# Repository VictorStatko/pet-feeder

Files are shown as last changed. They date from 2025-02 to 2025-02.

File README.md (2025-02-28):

# Pet Feeder

This project allows you to build an automated 3d printed pet feeder using an ESP32 microcontroller. It runs on a parallel 18650 battery pack. In my case, it works for about 2 months on a single charge. It supports scheduled feeding based on specified times and portion weights, sends Telegram notifications about all activities, and provides updates on the device's status, including battery percentage.

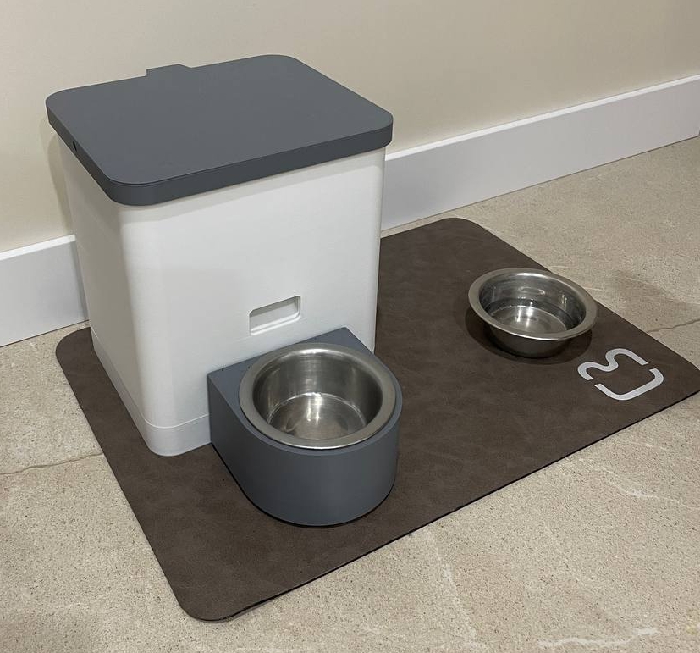
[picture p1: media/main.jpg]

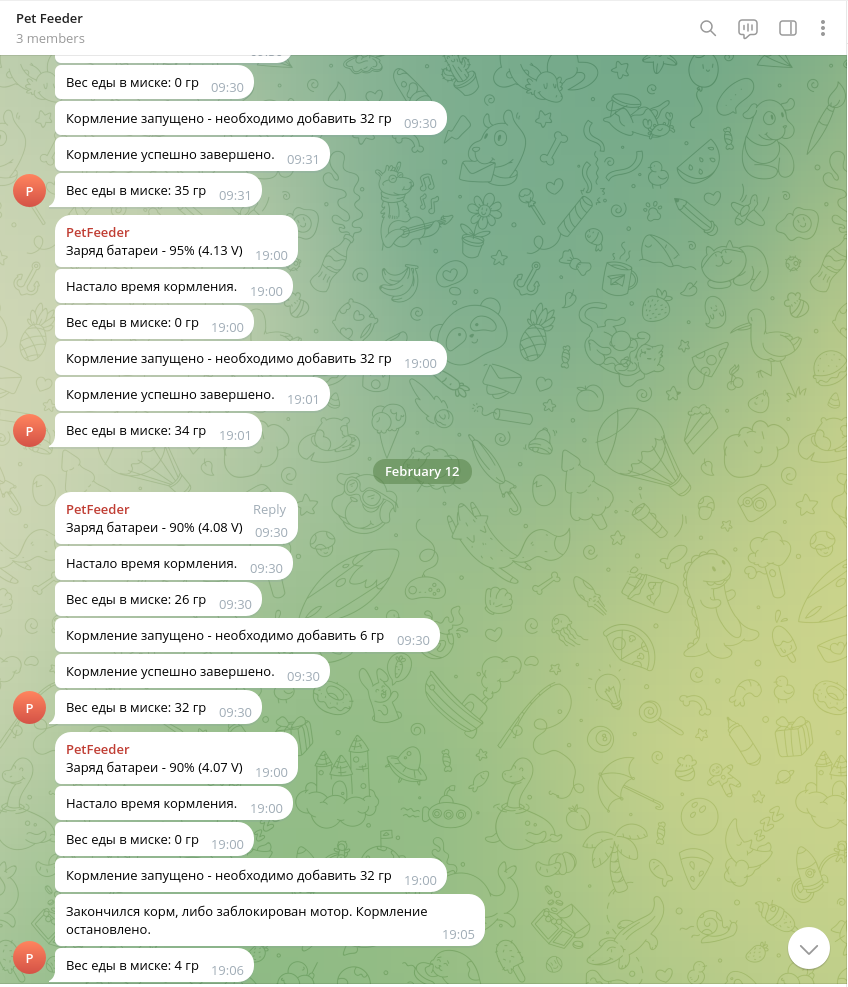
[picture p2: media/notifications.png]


https://github.com/user-attachments/assets/1bdc0e0a-baae-4a7a-a652-37525bfb75da

The approximate size of the feeder is 210 mm (width) x 180 mm (depth) x 240 mm (height). These dimensions can be modified as needed. All relevant files are included below.

In this configuration, the feeder holds approximately 1 kg of small-breed dog food.

## Hardware

1. ESP32 C3 (I used [TENSTAR ROBOT ESP32-C3](https://sl.aliexpress.ru/p?key=hEJPGh3))
2. DRV8833 DC Motor Driver (I used [WAVGAT DRV8833 Dual Motor Driver 1A](https://sl.aliexpress.ru/p?key=jnJPG1g))
3. DC Motor - 6V or lower (I used [JGA25-310 6V 20 RPM](https://sl.aliexpress.ru/p?key=jvJPGnO))
4. HX711 Weight Sensor + Load Cell (I used [1 KG load cell](https://sl.aliexpress.ru/p?key=o0JPGWY))
5. DS1302 RTC Module
6. Voltage Boost Converter (Something like the MT3608 will work, but I used a [UPS module](https://sl.aliexpress.ru/p?key=qwMPGBO) since I had a couple on hand)
7. Voltage Sensor (I used a [separate module](https://sl.aliexpress.ru/p?key=GOMPG0S), but just a couple of resistors would also work)
8. Power switch (I used a [double-pole switch](https://sl.aliexpress.ru/p?key=SGMPGXe) because I had it, but a simpler option would work too)
9. 18650 Parallel Pack Holder
10. Type-C Connector to power ESP32 C3 (Optional because there are other options, but I find it convenient to use)
11. Wago Connectors (Optional, but works for me - so why not)

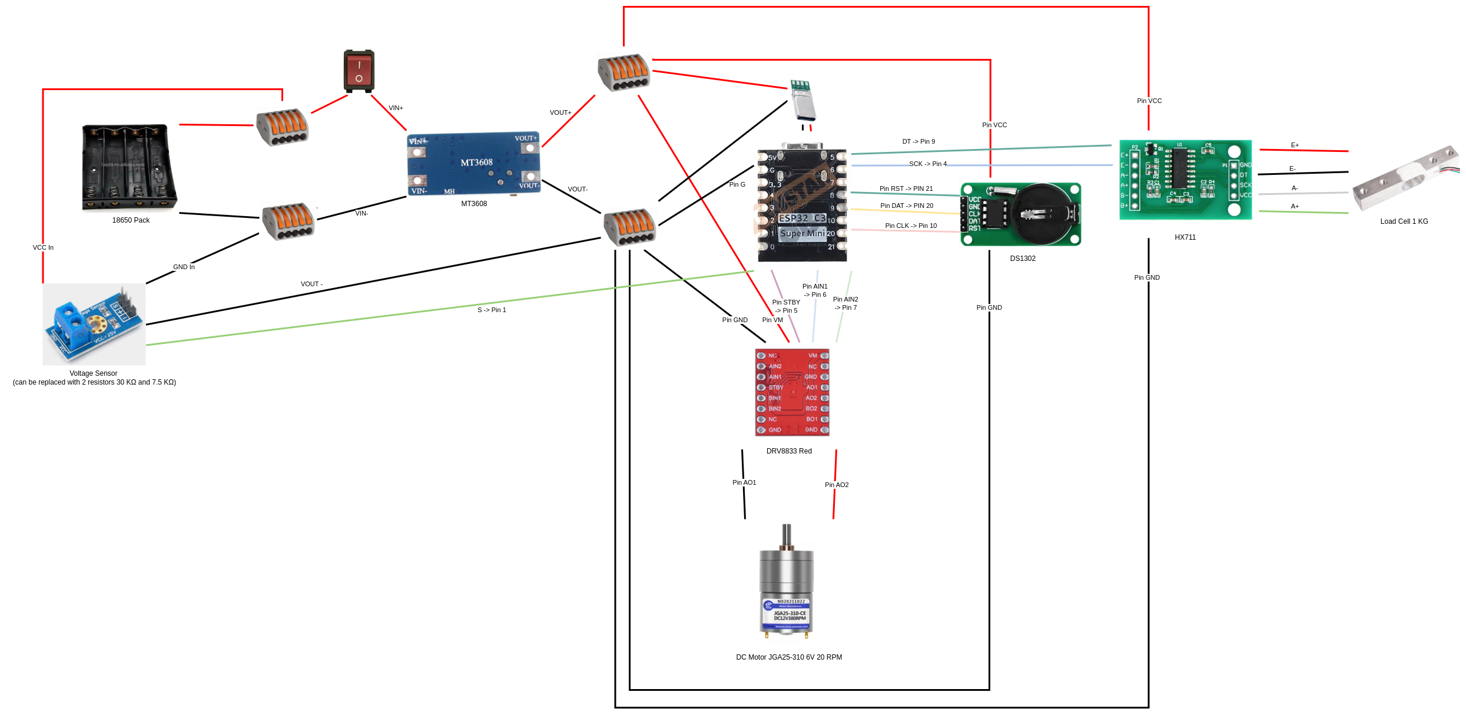
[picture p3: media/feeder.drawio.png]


## Model

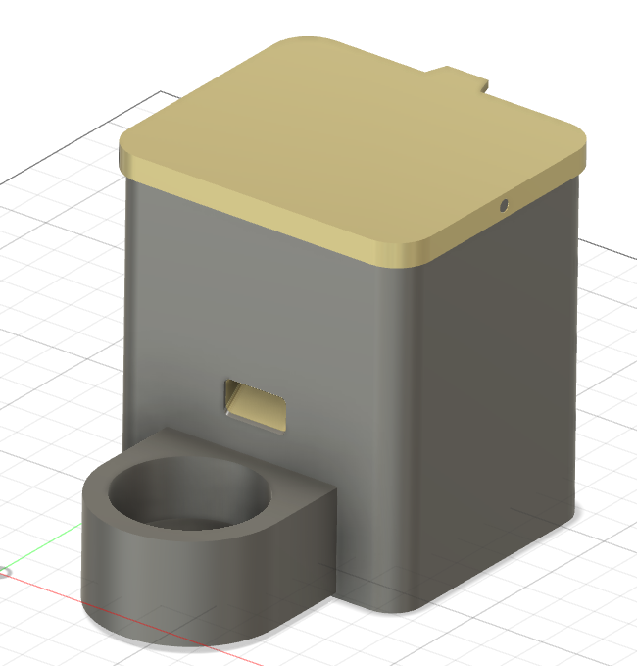
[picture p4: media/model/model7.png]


First of all, many thanks to Alexander Ulitin (https://github.com/ulitiy).

Initially, I planned to design the project from scratch, but I realized I was a bit lazy. So, I came across his awesome project (https://cubebrush.co/momwillbeproud/products/ndqc7a-5FoB/ultimate-3d-printed-pet-feeder) and decided to redesign it to better suit my needs.

Fusion file of redesigned project: [feeder.f3d](media/feeder.f3d)

Some screenshots can be found here: [model](media/model)

## Printed Parts

The feeder was printed using an Ender 3 V3 KE, which has a print size of 220 mm x 220 mm. Manual supports were used during the printing process. For additional hints and details about the printing process, please refer to the pictures here: [printedParts](media/printedParts)

## Assembly

Assembly photos can be found here: [assembly](media/assembly)

## Software

### 1. Install Arduino IDE
Set up the [Arduino IDE for ESP32](https://docs.espressif.com/projects/arduino-esp32/en/latest/installing.html) by following the official instructions.

### 2. Configure Partition Scheme
In the Arduino IDE, navigate to:
- **Tools** -> **Partition Scheme** -> **Huge App**.

### 3. Define Pins Used by the Feeder
Update the pin configuration in `feeder/UsedPins.h` according to your hardware setup.

### 4. Calibrate Load Cell (Step 1)
1. Open the file `additional/loadCellCalibration1` in the Arduino IDE.
2. Upload the sketch to the ESP32 and follow the Serial Monitor instructions.
3. Calculate the calibration factor using the formula:
   ```
   calibration factor = (reading) / (known weight)
   ```  
4. Save this calibration factor (e.g., `1106`).

### 5. Calibrate Load Cell (Step 2)
1. Open the file `additional/loadCellCalibration2` in the Arduino IDE.
2. Upload the sketch to the ESP32.  
   Perform this step after embedding the load cell into the 3D-printed enclosure (including the plate, but excluding the bowl).
3. Save the offset value obtained (e.g., `-62230`).

### 6. Configure Load Cell in Code
Include the retrieved calibration values in your code as follows:
```cpp
WeightSensor weightSensor(LOADCELL_DOUT_PIN, LOADCELL_SCK_PIN, 1106, -62230);
```

### 7. (Optional) Change Messages

Currently, all notification messages are provided only in Russian. If you want, you can change them - everything is in a single file:

**feeder/Messages.h**

### 8. Explore Additional Examples
In the `additional` folder, you’ll find example sketches for:
- **DC Motor Control**: Demonstrates how to control the motor used for dispensing food.
- **Load Cell**: Includes further examples for advanced load cell usage and testing.

Use these examples to better understand and customize specific components of the feeder.

### 9. Create a Telegram Bot
1. Open Telegram and search for **BotFather**.
2. Start a chat with **BotFather** and send the command `/newbot`.
3. Follow the instructions to set up your bot. You’ll receive a bot token upon completion.

### 10. Create a Telegram Group and Retrieve Group ID
1. Create a new Telegram group.
2. Add your bot and **@getidsbot** to the group.
3. Wait for **@getidsbot** to post a message containing the group ID. Copy the ID, then remove **@getidsbot** from the group.

### 11. Upload Code to ESP32
1. Open the main sketch for your feeder project in the Arduino IDE.
2. Connect your ESP32 to your computer via USB.
3. Select the correct **Board** and **Port** in the Arduino IDE:
   - **Tools** -> **Board** -> **ESP32 Dev Module**
   - **Tools** -> **Port** -> Select your ESP32's port.
4. Click **Upload** to flash the code onto your ESP32.

### 12. Connect ESP32 to Wi-Fi and Configure Feeder
1. When powered on, the ESP32 will broadcast an access point named **PetFeeder** with the password **11111111**.
2. Connect to this access point within 5 minutes to access the configuration portal.
3. Go to 192.168.4.1
4. Fill in the following details:
   - Wi-Fi credentials
   - Telegram bot token
   - Telegram group ID
   - Feeding schedule and portion weights

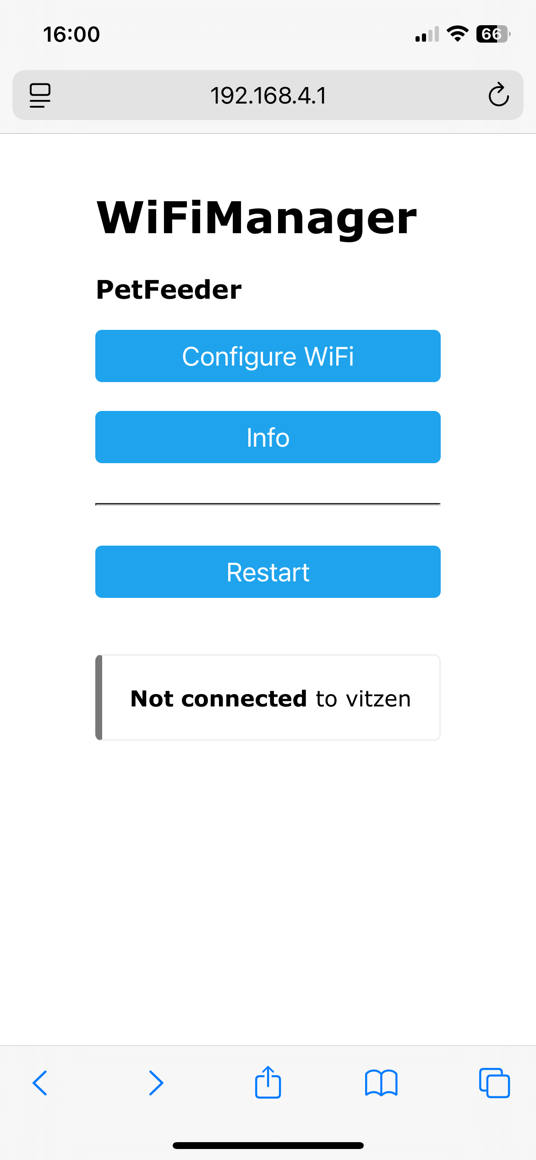
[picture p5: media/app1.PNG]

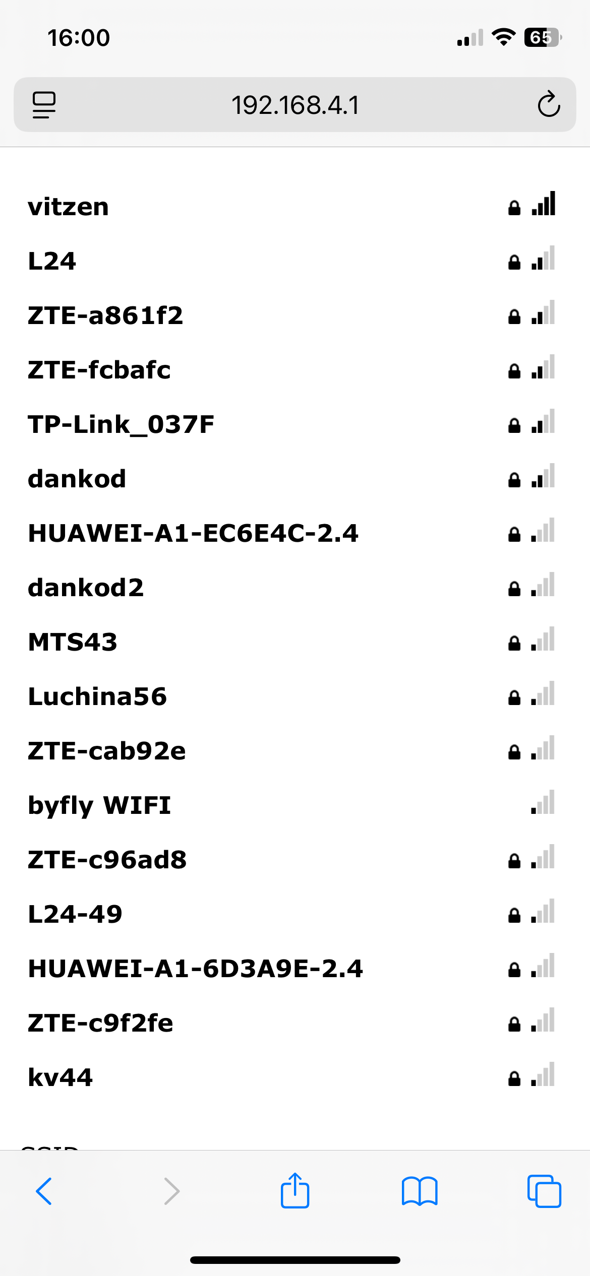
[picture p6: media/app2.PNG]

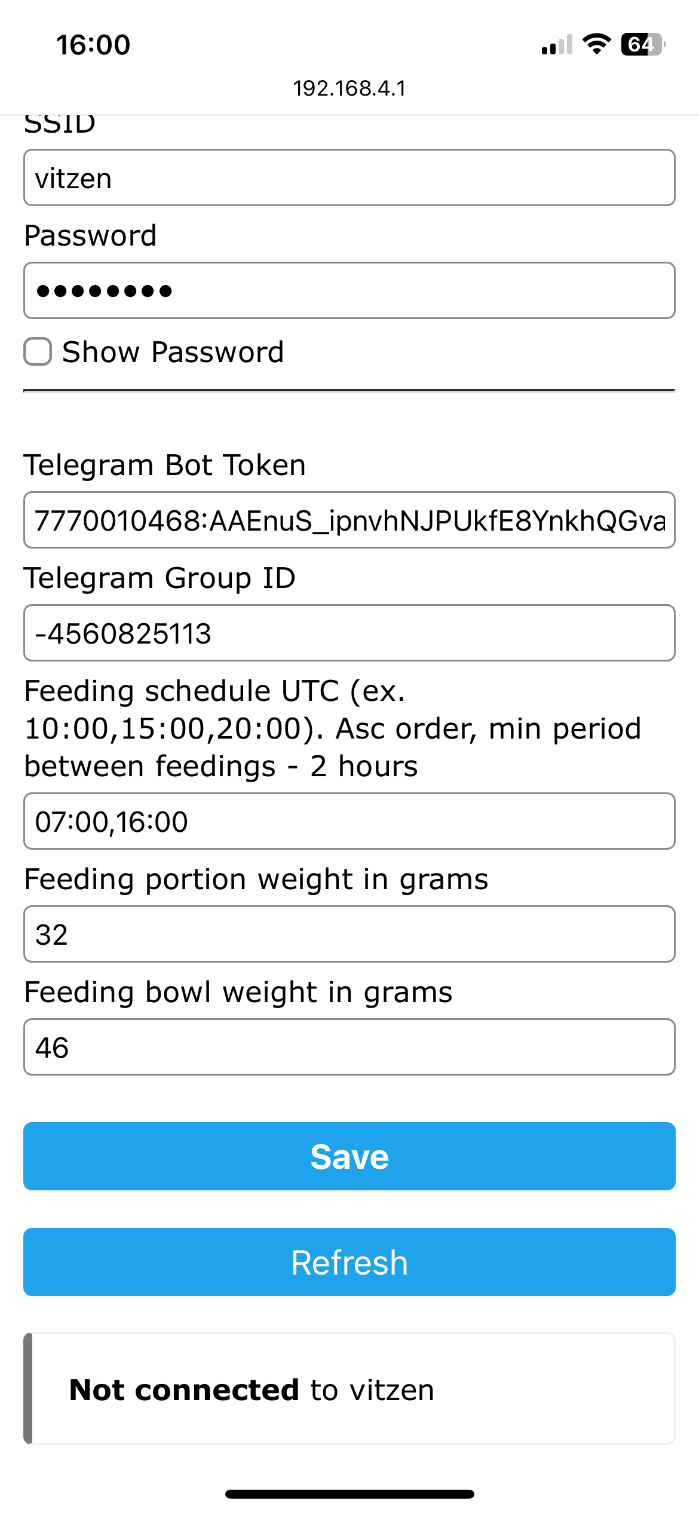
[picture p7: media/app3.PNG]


Once configured, the ESP32 will connect to Wi-Fi. You’ll receive a welcome message in your Telegram group either immediately upon successful connection or after the 5-minute configuration window expires.

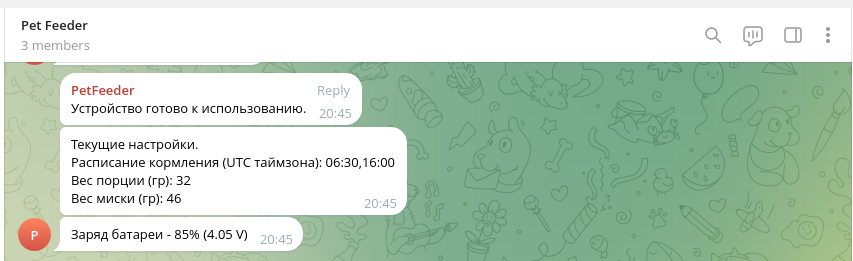
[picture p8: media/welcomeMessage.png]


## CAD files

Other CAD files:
media/feeder.f3d

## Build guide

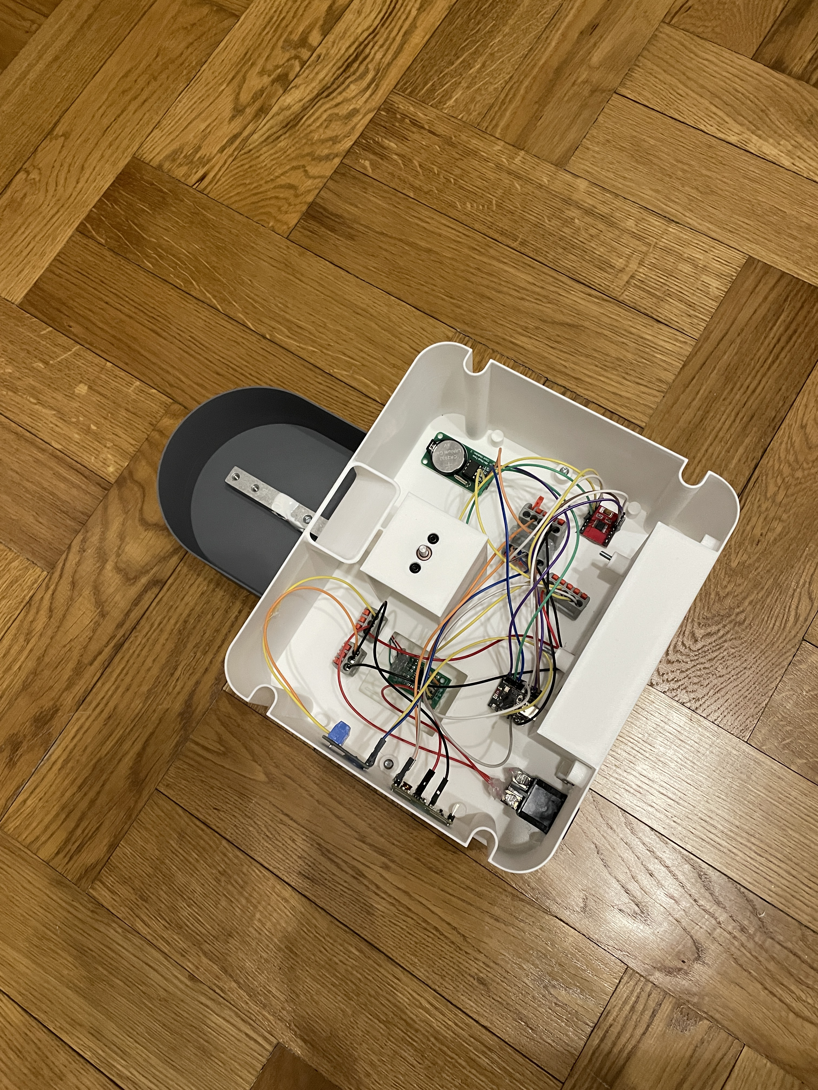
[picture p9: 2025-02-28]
media/assembly/4.JPG

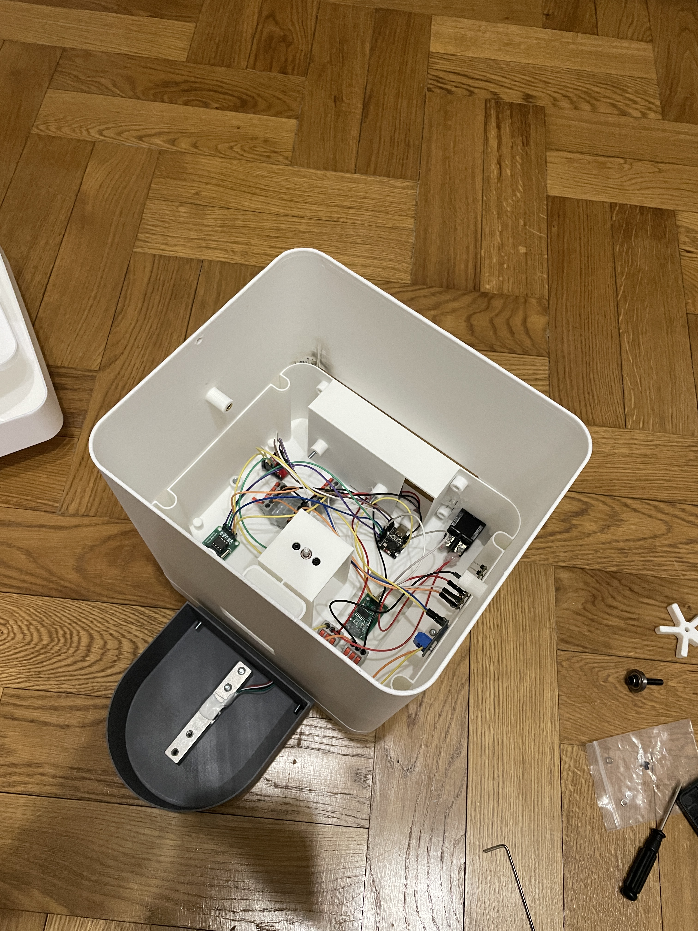
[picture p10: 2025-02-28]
media/assembly/6.JPG

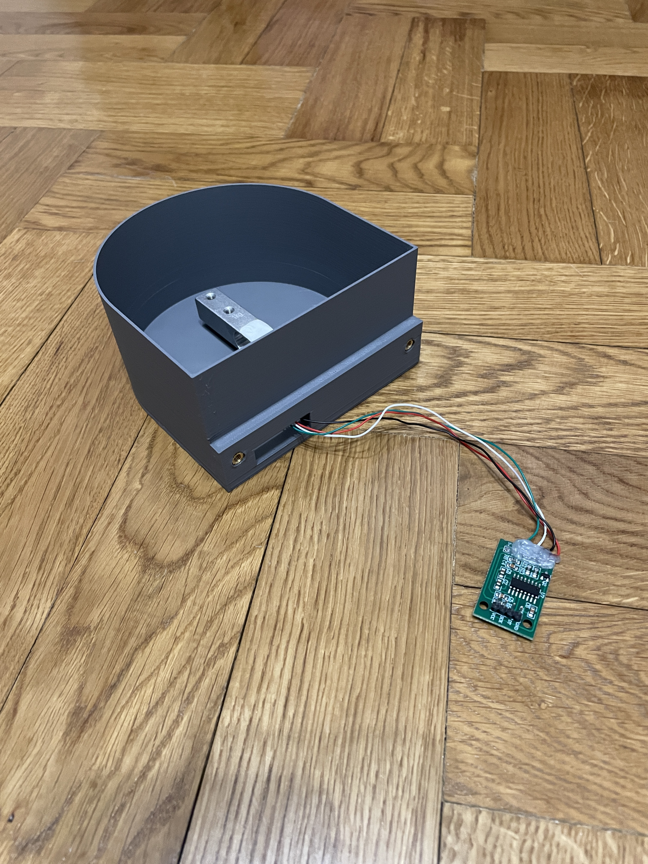
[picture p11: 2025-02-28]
media/assembly/1.JPG

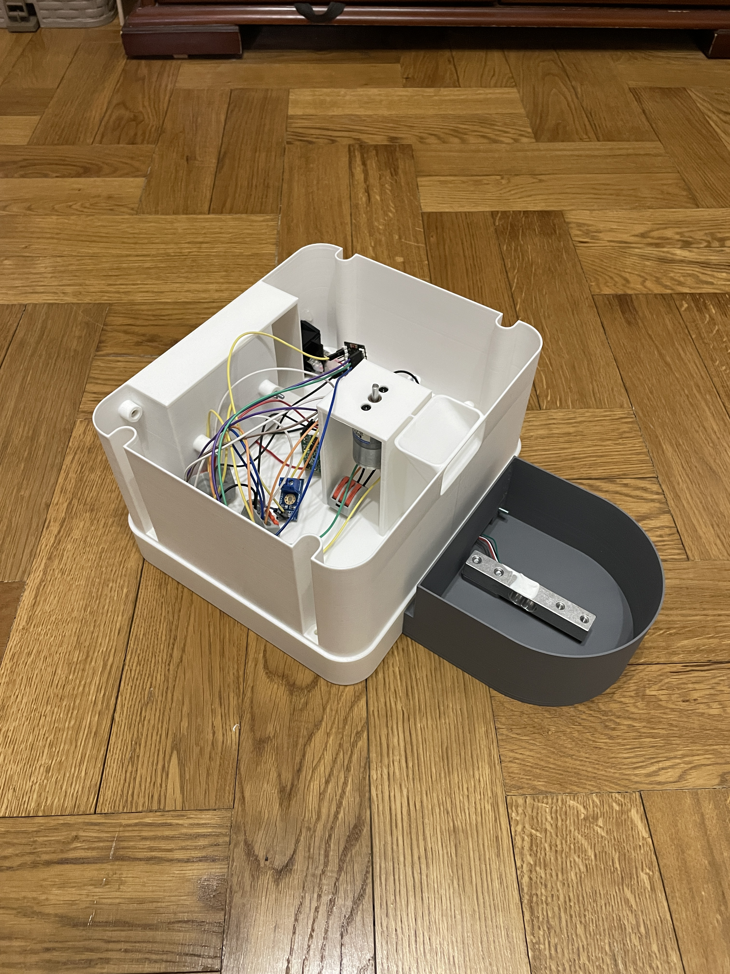
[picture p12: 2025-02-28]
media/assembly/3.JPG

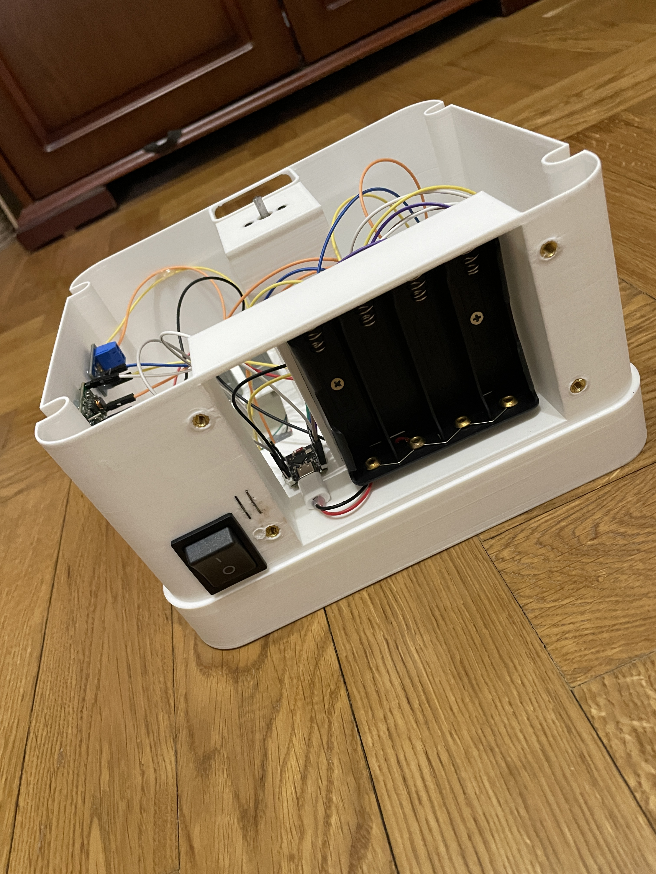
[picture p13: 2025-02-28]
media/assembly/5.JPG

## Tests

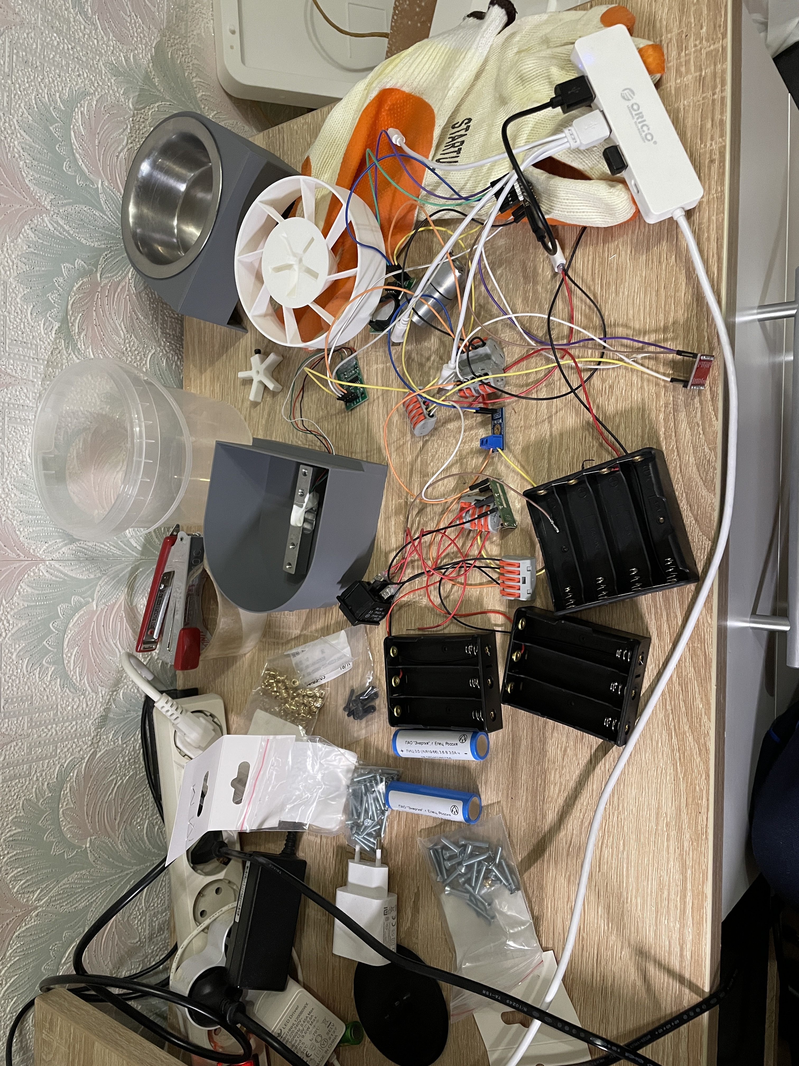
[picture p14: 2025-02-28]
media/assembly/testStand.JPG

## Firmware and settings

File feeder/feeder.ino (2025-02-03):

#include <Arduino.h>
#include "WiFiManagerWrapper.h"
#include "TelegramHandler.h"
#include <WiFi.h>
#include "ScheduleHandler.h"
#include "PreferencesHandler.h"
#include "VoltageSensor.h"
#include "WeightSensor.h"
#include "DCMotor.h"
#include "Messages.h"
#include "RtcModule.h"
#include "UsedPins.h"
#include <cmath>

// Persistent variables
RTC_DATA_ATTR bool initialSetupDone = false;

TelegramHandler telegramHandler;
RtcModule rtcModule(RTC_MODULE_DAT_PIN, RTC_MODULE_CLK_PIN, RTC_MODULE_RST_PIN, telegramHandler);
VoltageSensor voltageSensor(VOLTAGE_SENSOR_PIN);
WeightSensor weightSensor(LOADCELL_DOUT_PIN, LOADCELL_SCK_PIN, 1106, -62230);
DCMotor dcMotor(MOTOR_IN1_PIN, MOTOR_IN2_PIN, MOTOR_STBY_PIN);

// Setup function
void setup() {
  Serial.begin(115200);
  delay(1000);  // Allow Serial to stabilize
  Serial.println("Main - Device is waking up...");

  telegramHandler.begin(PreferencesHandler::getBotToken(), PreferencesHandler::getGroupId());
  rtcModule.begin();

  if (!initialSetupDone) {
    Serial.println("Main - Initial setup not done. Launching WiFiManager...");

    WiFiManagerWrapper::setupWiFiManager(telegramHandler);
    Serial.println("Main - WiFiManager setup completed.");

    WiFiManagerWrapper::autoConnectWiFi();
    Serial.println("Main - WiFi connection attempt executed.");

    rtcModule.sync();
    Serial.println("Main - RTC synchronization step executed.");

    telegramHandler.sendBotMessage(MESSAGE_READY_TO_USE);
    telegramHandler.sendBotMessage(
      MESSAGE_CURRENT_SETTINGS + "\n" + MESSAGE_CURRENT_SETTINGS_SCHEDULING + PreferencesHandler::getFeedingScheduleString()
      + "\n" + MESSAGE_CURRENT_SETTINGS_PORTION_WEIGHT + String(PreferencesHandler::getFeedingWeightPerPortion())
      + "\n" + MESSAGE_CURRENT_SETTINGS_BOWL_WEIGHT + String(PreferencesHandler::getFeedingBowlWeight()));
    telegramHandler.sendBotMessage(voltageSensor.getVoltageInfoMessage());

    initialSetupDone = true;
    Serial.println("Main - Initial setup completed and marked as done.");
  } else {
    Serial.println("Main - Initial setup already done. Skipping.");
  }
}

void goToDeepSleep(uint64_t seconds) {
  Serial.println("Main - Going to deep sleep for " + String(seconds) + " seconds...");
  delay(5000);                                       // For serial
  esp_sleep_enable_timer_wakeup(seconds * 1000000);  // Convert seconds to microseconds
  esp_deep_sleep_start();
}

int feedFood(int weightToFeed, int currentWeight) {
  Serial.println("Main - Starting food feeding process...");
  int previousWeight = currentWeight;
  int newWeight = -1;
  float newWeightFloat = -1;
  unsigned long lastWeightChangeTime = millis();

  bool weightSensorError = false;
  bool noWeightChangeError = false;
  bool success = false;

  while (true) {
    dcMotor.startMotor(false);
    delay(300);
    dcMotor.startMotor(true);
    delay(150);
    dcMotor.stopMotor();
    delay(1000);

    newWeightFloat = weightSensor.readWeight();

    if (std::isnan(newWeightFloat)) {
      Serial.println("Main - Error: Weight sensor not ready.");
      weightSensorError = true;
      break;
    } else {
      newWeight = floor(newWeightFloat);
    }

    if (newWeight > previousWeight + 2) {
      lastWeightChangeTime = millis();
      previousWeight = newWeight;
      Serial.println("Main - Weight increased. Updated previous weight: " + String(previousWeight));
    }

    if (millis() - lastWeightChangeTime > 300000) {
      Serial.println("Main - Stopping motor: No significant weight increase in the last 300 seconds.");
      noWeightChangeError = true;
      break;
    }

    if (newWeight >= currentWeight + weightToFeed) {
      Serial.println("Main - Stopping motor: Target weight reached.");
      success = true;
      break;
    }
  }

  if (weightSensorError) {
    telegramHandler.sendBotMessage(MESSAGE_WEIGHT_ERROR + MESSAGE_FEEDING_STOPPED);
    return -1;
  }

  if (noWeightChangeError) {
    telegramHandler.sendBotMessage(MESSAGE_FEEDING_NO_WEIGHT_CHANGE);
  }

  if (success) {
    telegramHandler.sendBotMessage(MESSAGE_FEEDING_SUCCESS);
  }

  return newWeight;
}

void startFeeding(time_t feedingTime) {
  Serial.println("Main - Feeding time! Activating feeder...");
  weightSensor.begin();
  dcMotor.begin();

  WiFiManagerWrapper::autoConnectWiFi();
  Serial.println("Main - WiFi connection attempt executed.");

  telegramHandler.sendBotMessage(voltageSensor.getVoltageInfoMessage());
  telegramHandler.sendBotMessage(MESSAGE_TIME_TO_FEED);

  int bowlWeight = PreferencesHandler::getFeedingBowlWeight();
  int weightPerPortion = PreferencesHandler::getFeedingWeightPerPortion();
  float initialWeightFloat = weightSensor.readWeight();

  if (std::isnan(initialWeightFloat)) {
    Serial.println("Main - Error: Weight sensor not ready.");
    telegramHandler.sendBotMessage(MESSAGE_WEIGHT_ERROR + MESSAGE_FEEDING_MISSED);
  } else {
    int initialWeight = floor(initialWeightFloat);
    int adjustedWeight = max(0, initialWeight - bowlWeight);

    if (initialWeight < bowlWeight / 2) {
      Serial.println("Main - No bowl. Feeding will not be executed.");
      telegramHandler.sendBotMessage(MESSAGE_NO_BOWL);
    } else {
      Serial.println("Main - Current weight of food: " + String(adjustedWeight));
      telegramHandler.sendBotMessage("Вес еды в миске: " + String(adjustedWeight) + " " + MESSAGE_GRAMM);

      int weightToFeed = weightPerPortion - adjustedWeight;

      if (weightToFeed <= 0) {
        Serial.println("Main - Current weight of food is enough. Feeding will be skipped.");
        telegramHandler.sendBotMessage(MESSAGE_FEEDING_ENOUGH_FOOD);
      } else {
        Serial.println("Main - Need to add the following amount of food (in grams): " + String(weightToFeed));
        telegramHandler.sendBotMessage(MESSAGE_FEEDING_START + String(weightToFeed) + " " + MESSAGE_GRAMM);

        int newWeight = feedFood(weightToFeed, initialWeight);

        if (newWeight != -1) {
          telegramHandler.sendBotMessage("Вес еды в миске: " + String(newWeight - initialWeight + adjustedWeight) + " " + MESSAGE_GRAMM);
        }
      }
    }
  }

  PreferencesHandler::saveLastFeedingTime(feedingTime);
  Serial.println("Main - Last feeding time saved.");

  weightSensor.end();
  dcMotor.end();
  Serial.println("Main - Feeding process completed and hardware turned off.");
}

// Main loop
void loop() {
  Serial.println("Main - Checking schedule for feeding time...");
  time_t now = rtcModule.getCurrentTime();

  std::vector<time_t> feedingTimes = ScheduleHandler::parseFeedingSchedule(now);
  time_t feedingTime = ScheduleHandler::shouldFeedNow(feedingTimes, now);

  bool feedNow = feedingTime != 0;

  time_t nextWakeup = ScheduleHandler::calculateNextWakeup(feedingTimes, now, feedNow);

  if (feedNow) {
    Serial.println("Main - Feeding time detected. Starting feeding process...");
    startFeeding(feedingTime);
    rtcModule.sync();
  } else {
    Serial.println("Main - Not feeding time yet. Next wakeup scheduled.");
  }

  goToDeepSleep(nextWakeup - now);
}

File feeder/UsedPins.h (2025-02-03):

#ifndef USED_PINS_H
#define USED_PINS_H

#include <Arduino.h>

const int VOLTAGE_SENSOR_PIN = 1;
const int RTC_MODULE_CLK_PIN = 10;
const int RTC_MODULE_DAT_PIN = 20;
const int RTC_MODULE_RST_PIN = 21;
const int LOADCELL_DOUT_PIN = 9;
const int LOADCELL_SCK_PIN = 4;
const int MOTOR_IN1_PIN = 6;
const int MOTOR_IN2_PIN = 7;
const int MOTOR_STBY_PIN = 5;

#endif

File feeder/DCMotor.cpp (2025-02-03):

#include "DCMotor.h"

DCMotor::DCMotor(int pinIn1, int pinIn2, int pinStby)
  : pinIn1(pinIn1), pinIn2(pinIn2), pinStby(pinStby) {
  Serial.println("DCMotor - Constructor initialized");
}

void DCMotor::begin() {
  Serial.println("DCMotor - Initializing pins and enabling motor standby mode");
  pinMode(pinIn1, OUTPUT);
  pinMode(pinIn2, OUTPUT);
  pinMode(pinStby, OUTPUT);

  digitalWrite(pinStby, HIGH);
  delay(1000);
  Serial.println("DCMotor - Initialization complete");
}

void DCMotor::end() {
  Serial.println("DCMotor - Stopping motor and disabling standby");
  digitalWrite(pinIn1, LOW);
  digitalWrite(pinIn2, LOW);
  digitalWrite(pinStby, LOW);
  Serial.println("DCMotor - Motor and standby disabled");
}

void DCMotor::startMotor(bool reverse) {
  Serial.println("DCMotor - Starting motor (IN1: HIGH, IN2: LOW)");
  if (reverse) {
    digitalWrite(pinIn1, LOW);
    digitalWrite(pinIn2, HIGH);
    Serial.println("DCMotor - Motor started (reverse)");
  } else {
    digitalWrite(pinIn1, HIGH);
    digitalWrite(pinIn2, LOW);
    Serial.println("DCMotor - Motor started");
  }
}

void DCMotor::stopMotor() {
  Serial.println("DCMotor - Stopping motor (IN1: LOW, IN2: LOW)");
  digitalWrite(pinIn1, LOW);
  digitalWrite(pinIn2, LOW);
  Serial.println("DCMotor - Motor stopped");
}

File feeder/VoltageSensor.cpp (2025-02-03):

#include "VoltageSensor.h"
#include "AnalogUtils.h"
#include "Messages.h"

VoltageSensor::VoltageSensor(int pin)
  : pin(pin) {}

float VoltageSensor::readRawVoltage() {
  const int attempts = 10;                  // Number of attempts
  const int readingsPerAttempt = 10;         // Number of readings per attempt
  const int delayBetweenAttemptsMs = 1000;  // Delay between attempts in milliseconds

  float totalVoltage = 0;

  for (int attempt = 0; attempt < attempts; ++attempt) {
    float attemptVoltage = 0;

    // Perform multiple readings for accuracy during this attempt
    for (int reading = 0; reading < readingsPerAttempt; ++reading) {
      int adcValue = AnalogUtils::readValue(pin);
      float adcVoltage = ((float)adcValue / 4095.0) * 3.3;
      attemptVoltage += adcVoltage * 5.0;
    }

    // Average the readings for this attempt
    attemptVoltage /= readingsPerAttempt;
    totalVoltage += attemptVoltage;

    delay(delayBetweenAttemptsMs);
  }

  // Return the average voltage across all attempts
  return totalVoltage / attempts;
}

float VoltageSensor::readVoltage() {
  return readRawVoltage();
}

int VoltageSensor::getBatteryPercentage(float batteryVoltage) {

  if (batteryVoltage >= 4.40) return 0;
  else if (batteryVoltage >= 4.20) return 100;
  else if (batteryVoltage >= 4.12) return 95;
  else if (batteryVoltage >= 4.05) return 90;
  else if (batteryVoltage >= 4.00) return 85;
  else if (batteryVoltage >= 3.95) return 80;
  else if (batteryVoltage >= 3.90) return 75;
  else if (batteryVoltage >= 3.85) return 70;
  else if (batteryVoltage >= 3.82) return 65;
  else if (batteryVoltage >= 3.78) return 60;
  else if (batteryVoltage >= 3.74) return 55;
  else if (batteryVoltage >= 3.70) return 50;
  else if (batteryVoltage >= 3.65) return 45;
  else if (batteryVoltage >= 3.60) return 40;
  else if (batteryVoltage >= 3.55) return 35;
  else if (batteryVoltage >= 3.50) return 30;
  else if (batteryVoltage >= 3.45) return 25;
  else if (batteryVoltage >= 3.40) return 20;
  else if (batteryVoltage >= 3.20) return 15;
  else if (batteryVoltage >= 3.00) return 10;
  else if (batteryVoltage >= 2.50) return 5;
  else return 0;
}

String VoltageSensor::getVoltageInfoMessage() {
  float voltage = readVoltage();
  int percentage = getBatteryPercentage(voltage);

  String percentageStr = (percentage != 0) ? String(percentage) + "%" : MESSAGE_UNKNOWN;
  return MESSAGE_BATTERY_PERCENTAGE + " - " + percentageStr + " (" + String(voltage) + " V)";
}

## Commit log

2024-11-27 voltage sensor
2024-11-28 remove adc multiplier; readme
2024-11-30 voltage multipliers
2024-12-02 fix load cell calibration (2)
    [loadCellCalibration2.ino]
2024-12-03 weight sensor
2025-02-27 readme - model and printed parts
    [feeder.f3d]
2025-02-28 Assembly instructions
